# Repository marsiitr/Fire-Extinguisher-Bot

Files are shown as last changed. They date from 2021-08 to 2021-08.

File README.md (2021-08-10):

<p align="justify">
<h1><b>Fire-Extinguisher-Bot</b></h1>
  <h2>Open Projects 2021</h2>
</p>

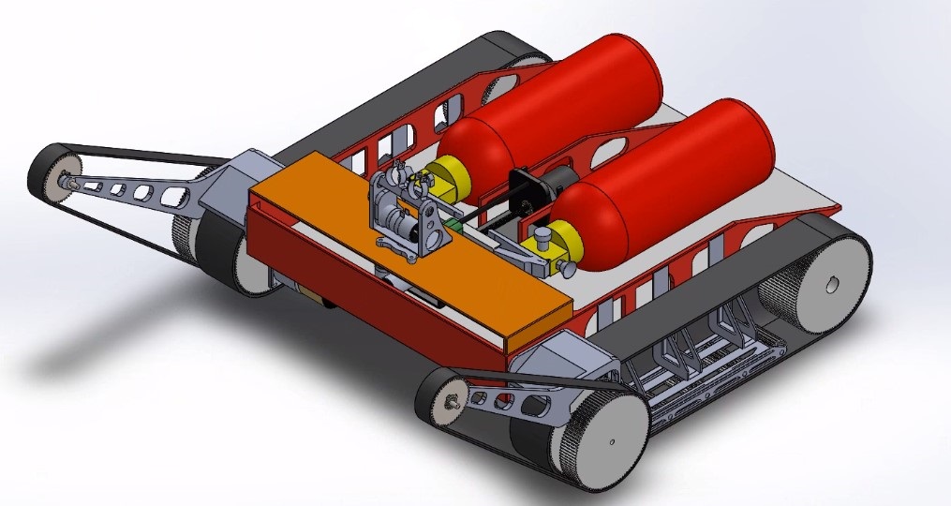
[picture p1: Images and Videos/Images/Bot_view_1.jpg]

<div align="center"><em>Bot View 1</em></div>
<br/>

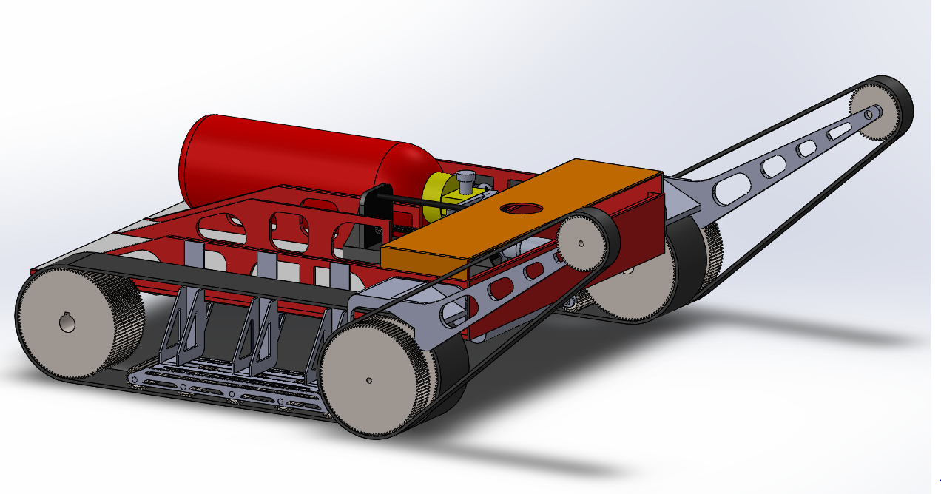
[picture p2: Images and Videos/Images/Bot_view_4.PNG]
Bot Design 2

<div align="center"><em>Bot View 2</em></div>
<br/>
 
<p align="justify">
  <h2>Abstract</h2>
</p>
<p align="justify">
  
- Automatic Fire Extinguisher Robot is a Hardware-based model used to put out the fire during fire accidents automatically. The Bot has features to move in the direction of fire  and extinguish it automatically.
- The Bot finds its applications in rescue operations during fire accidents where concerned authorities can take time to enter the fire-prone areas.
- Development of this autonomus bot using Controllers and image processing can help us to control fire without human inputs.Thus, minimising delays and unavailiblity of services.

</p>
 
<p align="justify">
  <h2>Motivation</h2>
</p>
<p align="justify">
  
The motivation behind this project essentially originated from our desire to learn new things. We can use this autonomous bot in case of laboratories or domestic fires, which can save lives or act as a quick remedy before the concerned authorities arrive. Although this technology is relatively unused in India, it can significantly impact the lives we lose to Fire incidents and our complete dependency on Emergency services.

</p>

<p align="justify">
  <h2>Mechanical Aspect of Design</h2>
</p>
<p align="justify">

The Mechanical Design is explicitly made for significant weight carrying capacity using mild steel as a material having composition of 0.20-0.30% Carbon and Manganese. It is sturdy and reliable and can easily transverse through domestic terrain.
The navigation of this can be both manual and automated. In the automatic mode, it is regulated via a PID Wall Following System.
> ## Wheel Assembly
> 
>The bot uses the Timing Belt Mechanism for the wheel Assembly. It provides an advantage of effortless mobility and significant weight carrying capacity over all the other mechanisms.

<p align="center">
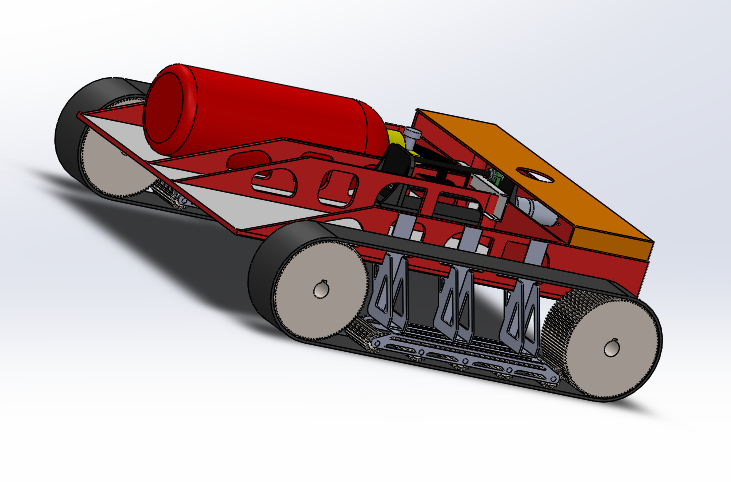
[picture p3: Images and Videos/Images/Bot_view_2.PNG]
  
  <br/><i>Timing Belt and Rollers</i>
</p>

> ## Nozzle Mechanism
> 
>The nozzle is a 2-axis gimbal. This Mechanism can rotate 30 degrees in both horizontal directions and 30 degrees in both vertical directions.

<p align="center">
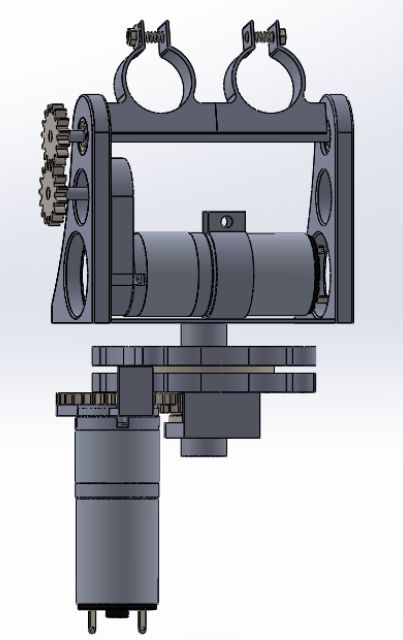
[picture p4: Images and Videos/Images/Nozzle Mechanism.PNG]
  
  <br/><i>Nozzle mechanism</i>
</p>

> ## Handle Pushing Mechanism
> 
>Leadscrew Mechanism can provide a torque of a considerable magnitude and resist the back force applied by the handle. Due to these factors, we use a leadscrew mechanism for handle pushing in our bot.

</p>
<p align="center">
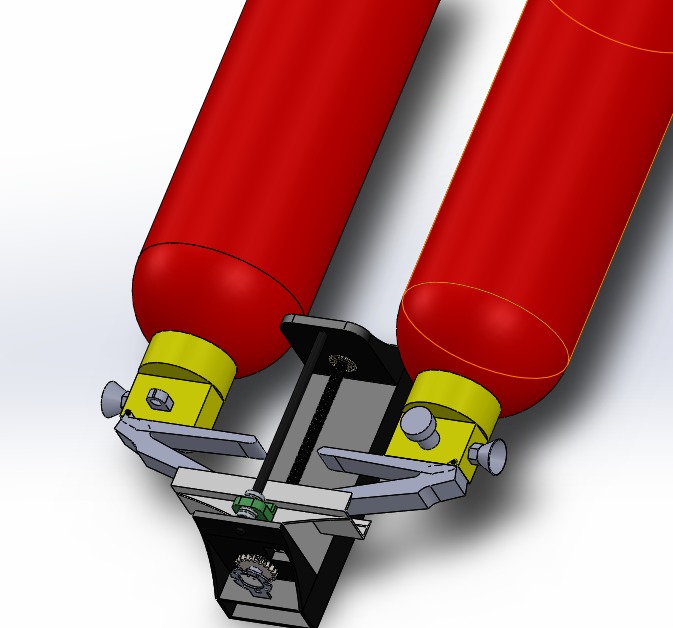
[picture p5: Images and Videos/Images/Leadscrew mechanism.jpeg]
  <br/>
  <i>Leadscrew mechanism</i>
</p>
<p align="justify">
 
> ## Stair Climbing
> 
>The stair climbing mechanism works based on two-timing belts, positioned at an angle of 23 Degrees from the ground. We decided on this angle after a brief round of simulation on coppeliasim.

</p>
<p align="center">
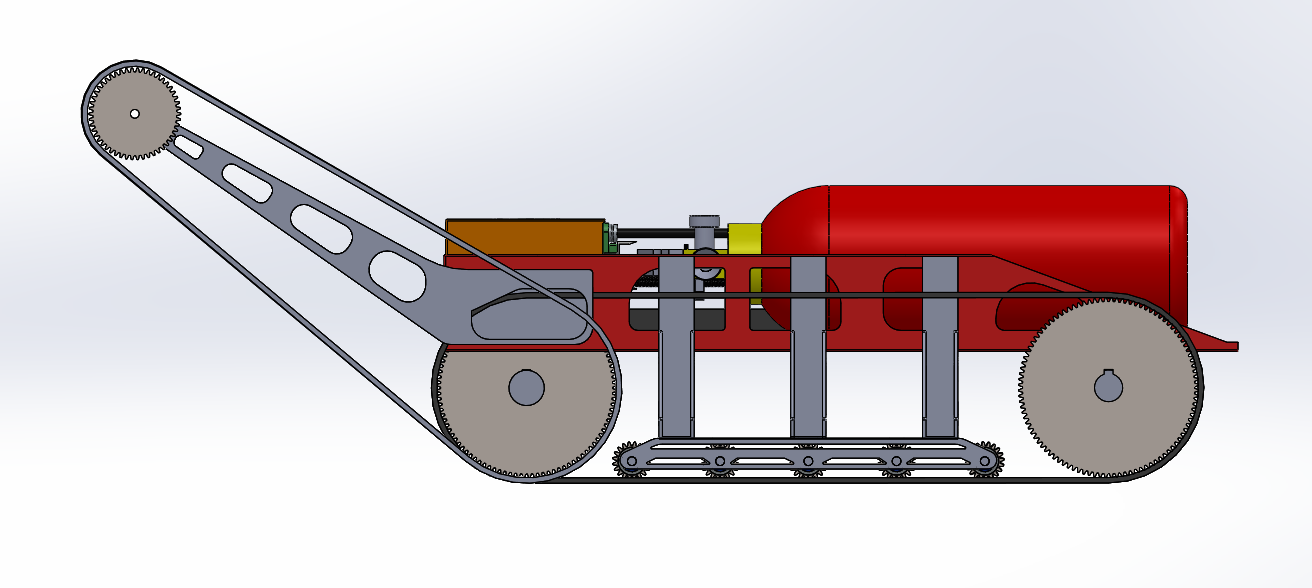
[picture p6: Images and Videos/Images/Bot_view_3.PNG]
  
  <br/><i>Wheel assembly</i>
</p>
<p align="justify">
  <h2>Electrical Aspect of Design</h2>
</p>
<p align="justify">
  
- We used microcontrollers for BOT movement and nozzle movement.

<p align="center">
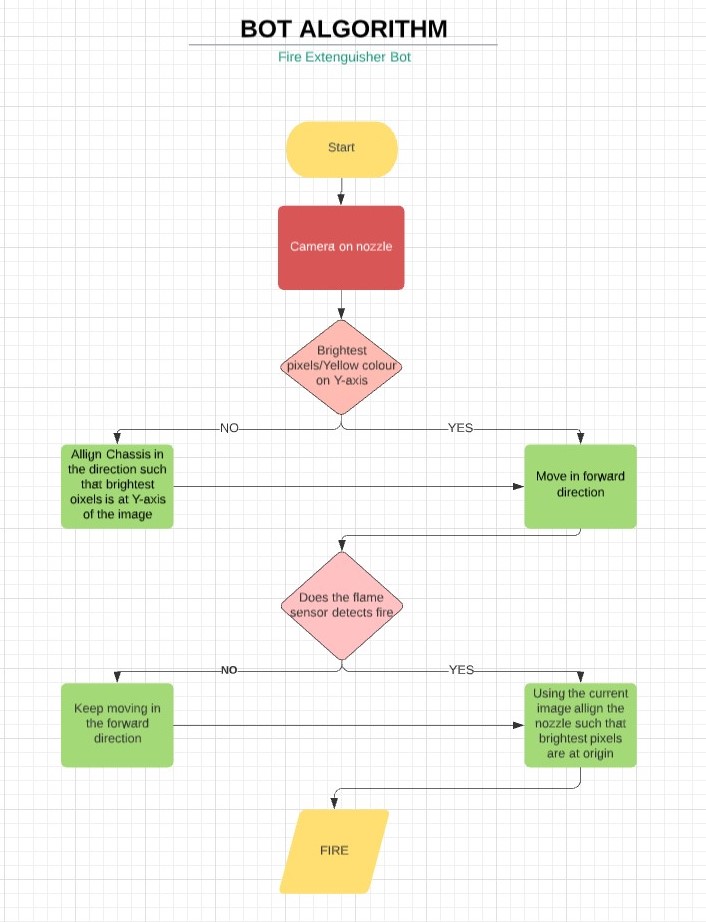
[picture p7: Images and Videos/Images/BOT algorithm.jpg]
  <br/>
  <i>BOT algorithm</i>
</p>

- We also used Ultrasonic distance sensors, Temperature sensors and Flame sensors.
<br/>

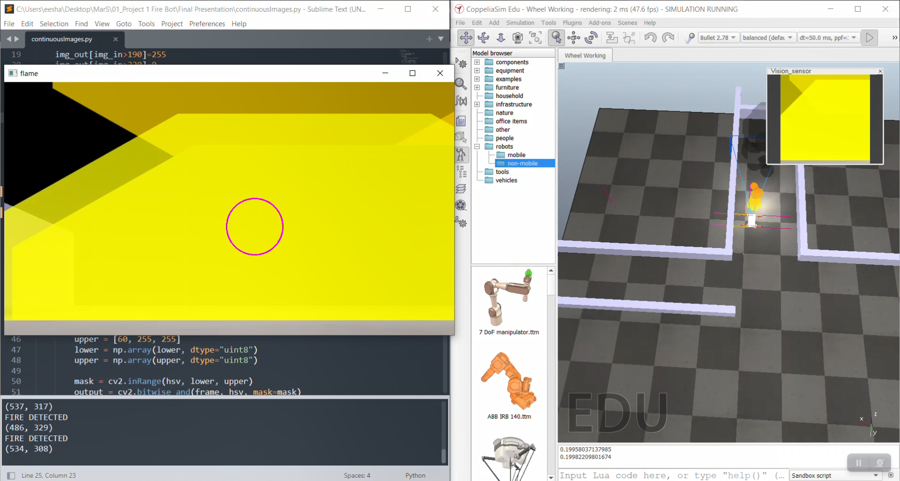
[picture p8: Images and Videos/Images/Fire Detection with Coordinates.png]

<div align="center"><em>simulation</em></div>
<br/>

- For image processing we used camera (*as a Hardware part*). The image processing Software used is OpenCV. The data about the image is fed to OpenCV, where the image is converted to HSV and GreyScale format. Approximate Centre Coordinates of the fire are calculated. This Data is then stored in a text file for the simulation software or Audrino to use.
<br/>

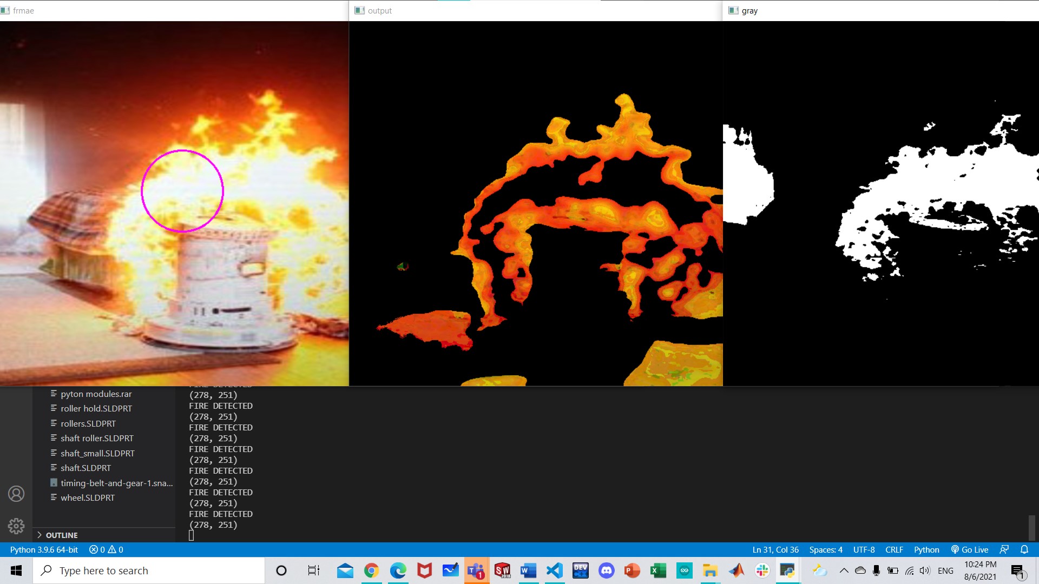
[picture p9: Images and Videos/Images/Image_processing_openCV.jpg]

<div align="center"><em>Image processing</em></div>
<br/>
</p>

<p align="justify">
  <h2>Simulation</h2>
</p>
<p align="justify">
  
For simulation purpose we used the following softwares :-
- Solidworks
    > For mechanical designing of our BOT.
- Tinkercad
    > For simulating Temperature sensor working.
- Coppeliasim
    > For simulating Stair climbing, Wall detection, Wheel PID and Fire detection.
- Python and openCV
    > For Image processing to detect fire and marking that center of fire (high intensity zone) with circle. 

For elaborative explanation, you can refer [here](https://github.com/Ch0ubey/Fire-Extinguisher-Bot/blob/49c68fb09d31af3eed7d412b4f8d0a11268a28de/Simulation/README.md).

</p>
<p align="justify">
  <h2>Applications</h2>
</p>
<p align="justify">
  
- The main objective of the fire extinguishing bot is to search for the fire and put it off. Sensors are used to evaluate the environment in which the bot is operating and allows the bot to adjust actions based on collected data. The buzzer used will be helpful in alarming people about the danger.
- As it is an autonomus bot which uses Controllers and image processing, so it can help us to control fire without human inputs.
- Using this bot we can minimise delays and unavailiblity of services during emergency.
- It can be highly useful in extinguishing fire where probability of explosion is high. For eg. Hotel kitchens, LPG/CNG gas stores, etc.

</p>
<p align="justify">
  <h2>Cost Structure</h2>
</p>

| Components |Amount(INR)  | Quantity |  Cost(INR) |
|--- |:---:|:---: |---:|
| Ultrasonic sensors |  75 |  7 |  525 |
| Temperature sensors |  75 |1 |  75 |
| Flame sensors | 59 |1 |  59 |
| Camera| 300 | 1|  300|
|Arduino UNO|500|1| 500|
|Encoder|1500|1| 1500|
|Dc motors|1500|1| 1500|
|Lead screw|100|1| 100|
|Timing belt (G/GB type) | 400| 1 |400|
|Wheels(lower) |480| 6|2880|
|Wheels(upper)|320 | 2|640|
|3D Printing Filament| 1200|1|1200|
|Fire extinguisher (ABC powder 4kg)|1000|2|2000|
|Mild steel (Body material)|50|2|100|
|**Total Cost**| | |**11,699**|

<p align="justify">
  <h2>Limitations</h2>
</p>

- Takes time to detect fire
- Needs manual assistance while changing the fire extinguishers
- Usable for household fires only
<p align="justify">
  <h2>Future Improvement</h2>
</p>
<p align="justify">
 
* Install cameras in every room
* Link with smoke sensors in the area
* Use custom made cylinders to avoid manual assistance

 </p>
<p align="justify">
  <h2>Team members</h2>
</p>
<p align="justify">

1. [Akanksha Vijayvergiya](https://github.com/Akanksha-247)
2. [Eeshan Punde](https://github.com/eeshanpunde14)
3. [Ganesh Kalanidhi](https://github.com/GaneshK-RKE)
4. [Mritunjay Kumar Choubey](https://github.com/Ch0ubey)
5. [Poreddy Sahith Reddy](https://github.com/sahithreddyporeddy)
6. [Srushti Parbat](https://github.com/SrushtiParbat)

</p>  
<p align="justify">
  <h2>Mentors</h2>
</p>
<p align="justify">

1. [Naman Agarwalla](https://github.com/naman99-agar)
2. [Parul Chaudhary](https://github.com/Parul253)
3. [Shubham Goyal](https://github.com/shubham491981)

</p>
<p align="justify">
  <h2>Refrences link</h2>
</p>
<p align="justify">
  
- [Coppeliasim Tutorial](https://www.youtube.com/watch?v=PwGY8PxQOXY&list=PLjzuoBhdtaXOoqkJUqhYQletLLnJP8vjZ)
- [Solidworks Tutorial](https://youtube.com/playlist?list=PLkMYhICFMsGajeARsY7N1t1jhbtMb1poL)
- [2 axis gimbal](https://www.youtube.com/watch?v=i6UoxhNlr1U)
- [Image processing openCV](https://www.youtube.com/watch?v=Z78zbnLlPUA&list=PLQVvvaa0QuDdttJXlLtAJxJetJcqmqlQq)
- [Coppeliasim Documentation](https://www.coppeliarobotics.com/helpFiles/index.html)

  </p>

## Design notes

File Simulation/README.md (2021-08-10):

<p align="justify">
<h1><b>Running the simulation</b></h1>
  <h2>stair climbing</h2>
</p>

### Installation
<p align="justify">
We used coppeliasim as our simulating software. So, First of all you will have to install it.
</p>

> [CoppeliaSim V4.2.0 rev5 for Windows](https://www.coppeliarobotics.com/files/CoppeliaSim_Edu_V4_2_0_Setup.exe)
### Execution
<p align="justify">

- Download and open the file named "STAIR CLIMBING.ttt".
</p>

  > [STAIR CLIMBING.ttt](https://github.com/Ch0ubey/Fire-Extinguisher-Bot/blob/7c658c72f4b91b798972f8a7e9d713d7e336b766/Simulation/STAIR%20CLIMBING.ttt)

<p align="justify">
  
- Run the simulation by clicking on that play simulation option (As marked in Fig.).
    > <p align="center">
  <br/>
</p>
</p>

## Wheel PID and Fire detection
### Installation

<p align="justify">
  
We used coppeliasim as our simulating software. So, First of all you will have to install it.
</p>

> [CoppeliaSim V4.2.0 rev5 for Windows](https://www.coppeliarobotics.com/files/CoppeliaSim_Edu_V4_2_0_Setup.exe)
<p align="justify">
  
For Image processing part you will have to install python and openCV libraries.
</p>

> [Python 3.9.6 64-bit](https://www.python.org/ftp/python/3.9.6/python-3.9.6-amd64.exe)

> [Tutorial video](https://youtu.be/d3AT9EGp4iw)
### Execution
<p align="justify">
  
- Download and open the file named "Wheel PID and Fire detection.ttt" and "Image processing.py" (Using any IDE).
</p>

   > [Wheel PID and Fire detection.ttt](https://github.com/Ch0ubey/Fire-Extinguisher-Bot/blob/7c658c72f4b91b798972f8a7e9d713d7e336b766/Simulation/Wheel%20PID%20and%20Fire%20detection.ttt)
   
   > [Image processing.py](https://github.com/Ch0ubey/Fire-Extinguisher-Bot/blob/7c658c72f4b91b798972f8a7e9d713d7e336b766/src/Image%20processing.py)
 
 <p align="justify">
  
 - Take any image file and make sure that it should be in the same folder where "Image processing.py" is. Then, paste that image file name on the marked location (Shown in Img.).
    > [Sample image file](https://github.com/Ch0ubey/Self/blob/989c6f968e18636200eb5e8f460e3fbb0165312d/L.jpeg)
    > <p align="center">
  <br/>
</p>
</p>
<p align="justify">
  
- Open that coppeliasim file named "Wheel PID and Fire detection.ttt" and click on that Dummy script option.
      <p align="center">
  <br/>
</p>
</p>
<p align="justify">
  
- Now, change that path location to the samale image you have taken previously.
       <p align="center">
  <br/>
</p>
</p>
<p align="justify">

- Finally, Run the simulation by clicking on that play simulation option (As marked in Fig.).
       <p align="center">
  <br/>
</p>
</p>
<p align="justify">
  
- Also, Run that python file named "Image processing.py" to get centre detection of fire.
</p>

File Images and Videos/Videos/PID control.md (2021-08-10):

# **PID Control**
[PID Control Video](https://drive.google.com/file/d/1zevA3bUyDVg1U9erdCAcblWegYRJz-ra/view?usp=sharing)

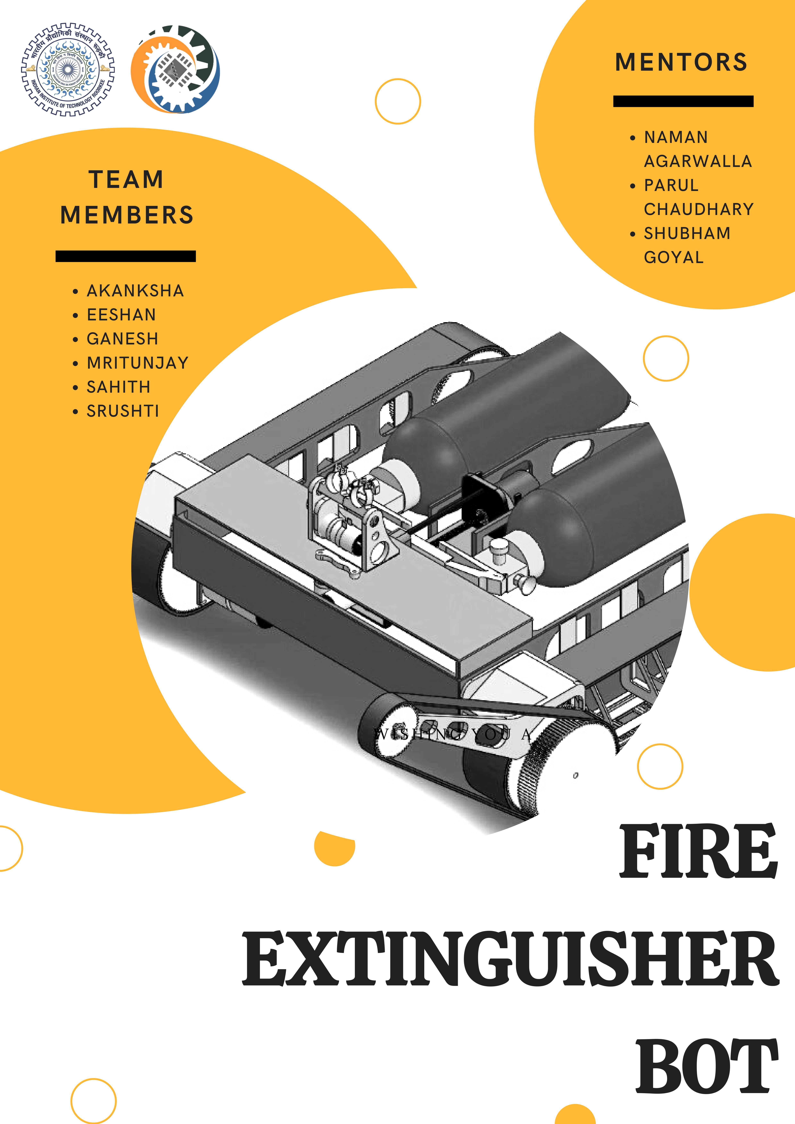
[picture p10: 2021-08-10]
Poster and report/Poster.jpeg

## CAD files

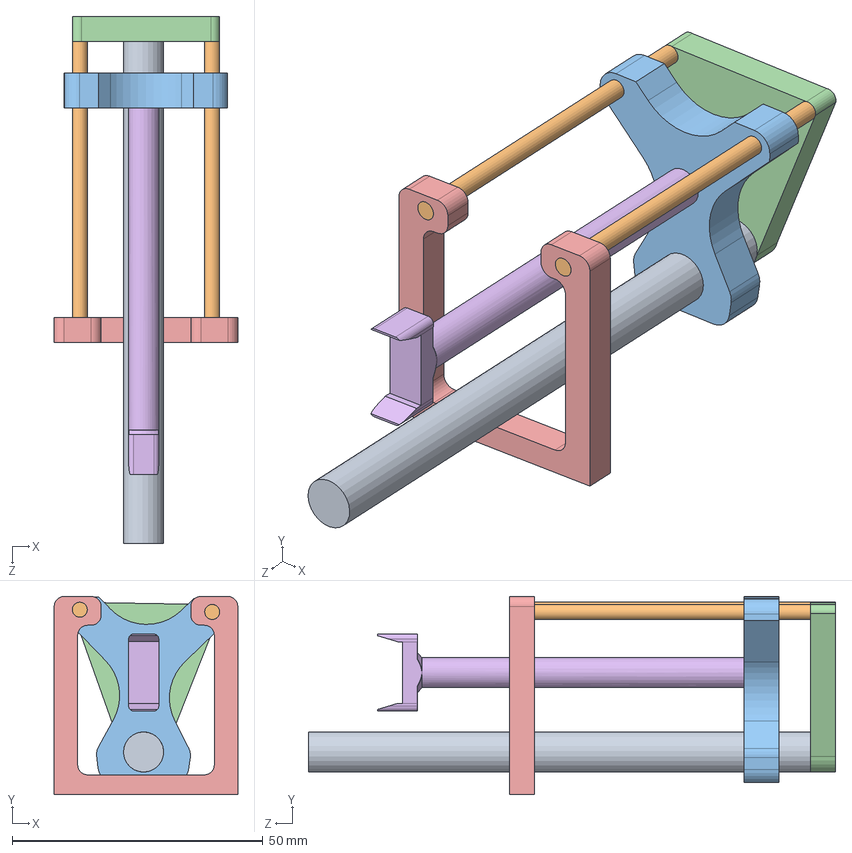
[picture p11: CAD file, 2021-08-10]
Mechanical Design/Bot SolidWorks files/Assem121.SLDASM
36.6 x 39.5 x 105.0 mm
Partscrew
Partrod x 2
Partbase
Part1^Assem121
Part5^Assem121
Partrod33

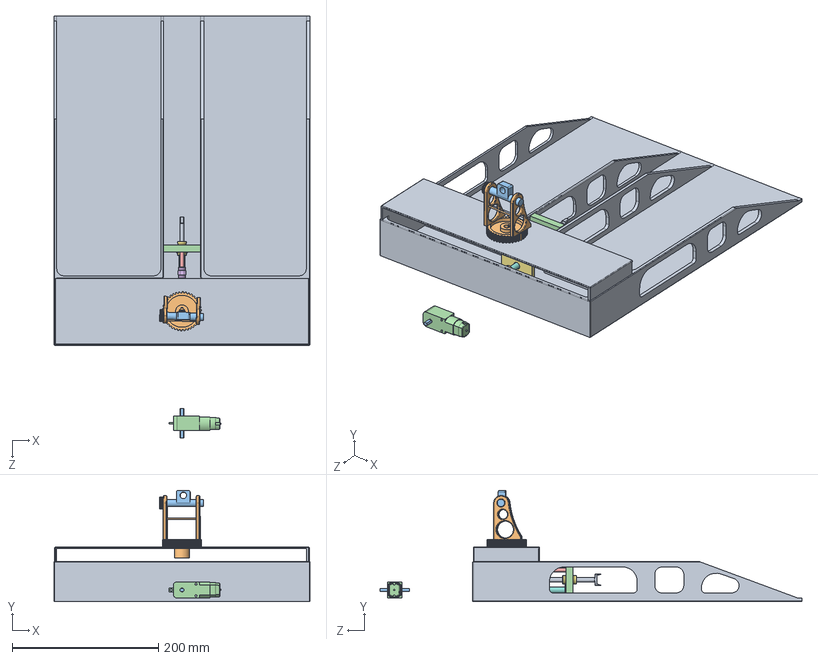
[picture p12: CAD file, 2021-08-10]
Mechanical Design/Bot SolidWorks files/1111.SLDASM
350.0 x 152.2 x 576.4 mm
Part3^1111
Part4^1111
Part5^1111
Part7^1111
Partrod33
Part8^1111
Eje
Motor sin eje
Ball Bearing F695ZZ x 2
ball_bearing_lm5uu
ball_bearing_lm6uu

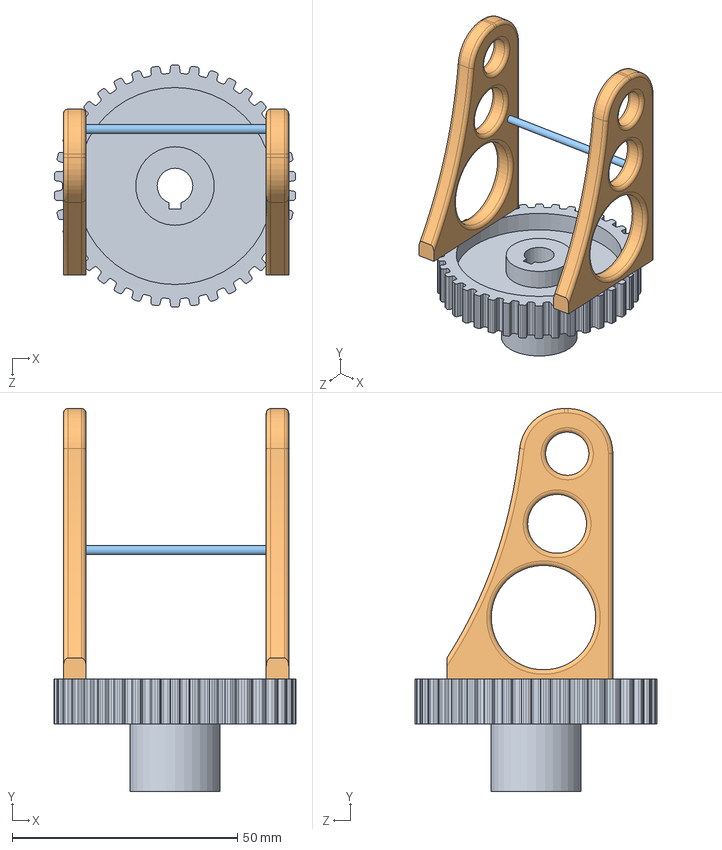
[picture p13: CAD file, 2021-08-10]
Mechanical Design/Bot SolidWorks files/Assem1.SLDASM
53.6 x 85.0 x 53.7 mm

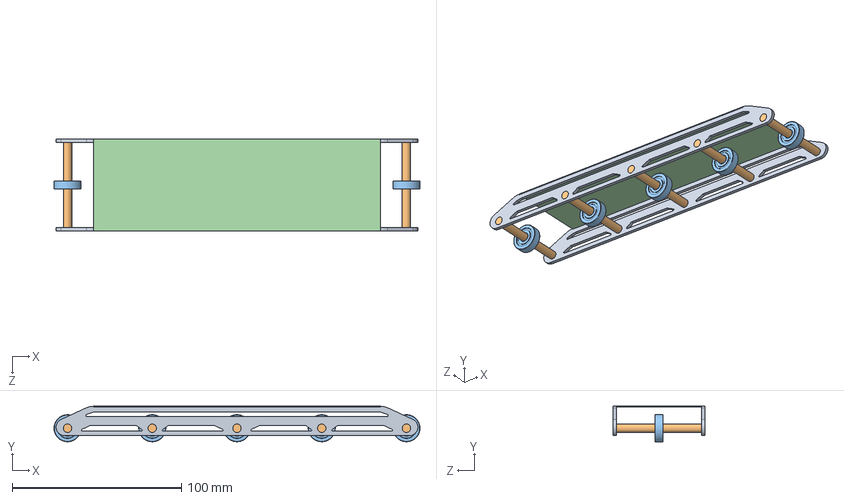
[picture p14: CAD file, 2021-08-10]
Mechanical Design/Bot SolidWorks files/Assem13.SLDASM
216.0 x 21.0 x 54.0 mm
Part16^Assem13
5mm Bearing SKF 625 RS 286-7811 x 5
Part19^Assem13

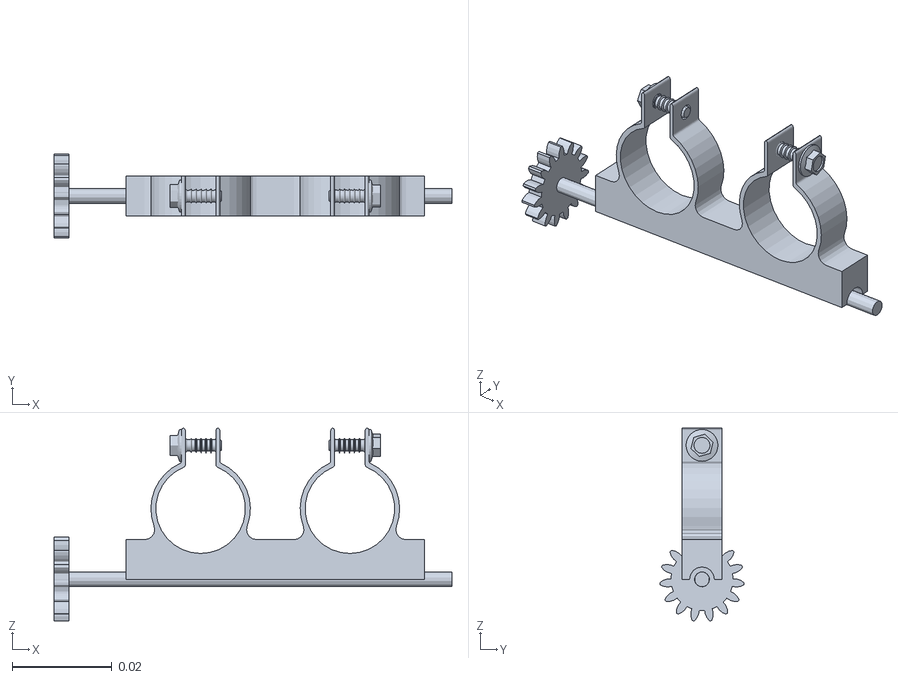
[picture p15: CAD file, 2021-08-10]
Mechanical Design/Bot nozzle/meshes/upper nozzle 0101.STL
0.08 x 0.0169 x 0.0388

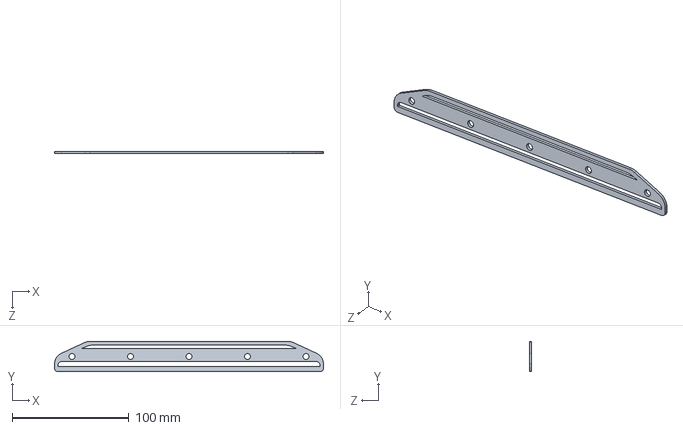
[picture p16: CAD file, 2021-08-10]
Mechanical Design/Bot SolidWorks files/Part15.SLDPRT
230.0 x 26.0 x 2.00 mm

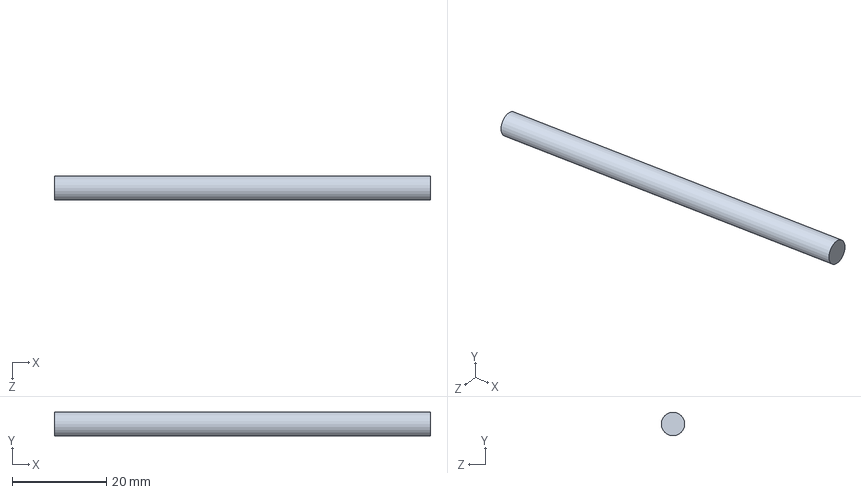
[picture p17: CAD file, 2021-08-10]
Mechanical Design/Bot SolidWorks files/Part2.SLDPRT
80.0 x 5.00 x 5.00 mm

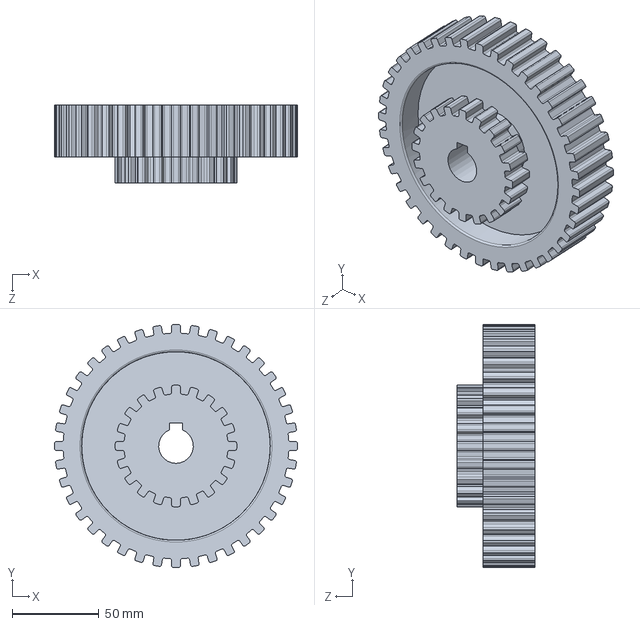
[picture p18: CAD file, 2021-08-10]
Mechanical Design/Bot SolidWorks files/Part10.SLDPRT
140.0 x 140.0 x 45.0 mm

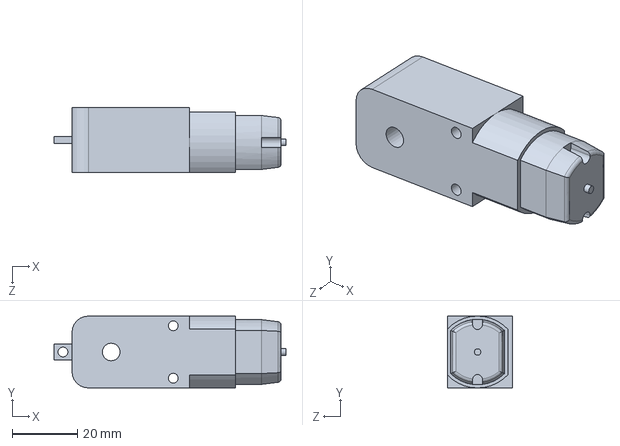
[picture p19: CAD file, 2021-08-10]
Mechanical Design/Bot SolidWorks files/Motor sin eje.SLDPRT
71.0 x 22.0 x 20.0 mm

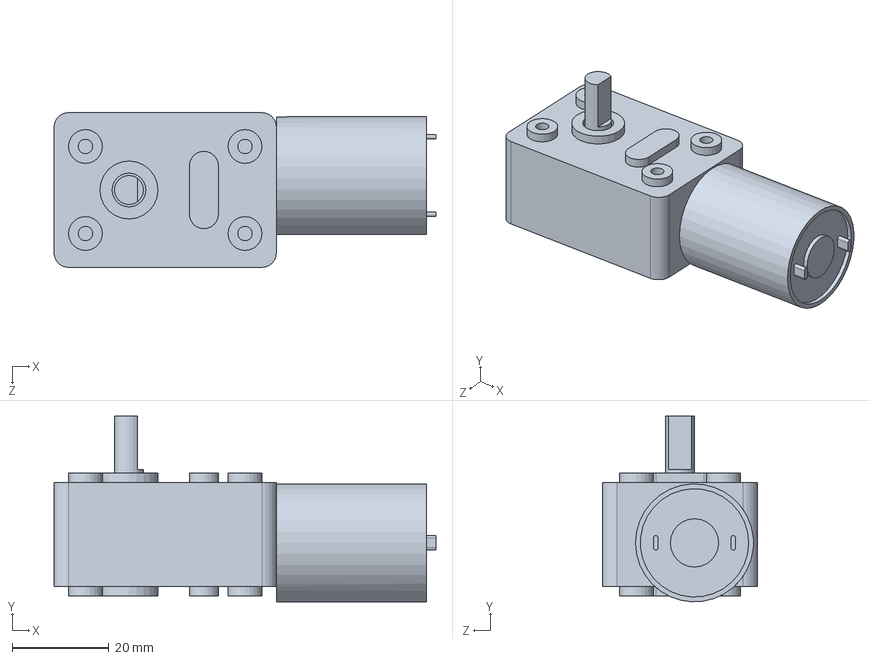
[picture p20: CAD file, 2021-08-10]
Mechanical Design/Bot SolidWorks files/12v_DC_Gearmotor_5-60rpm.SLDPRT
79.0 x 38.4 x 32.0 mm

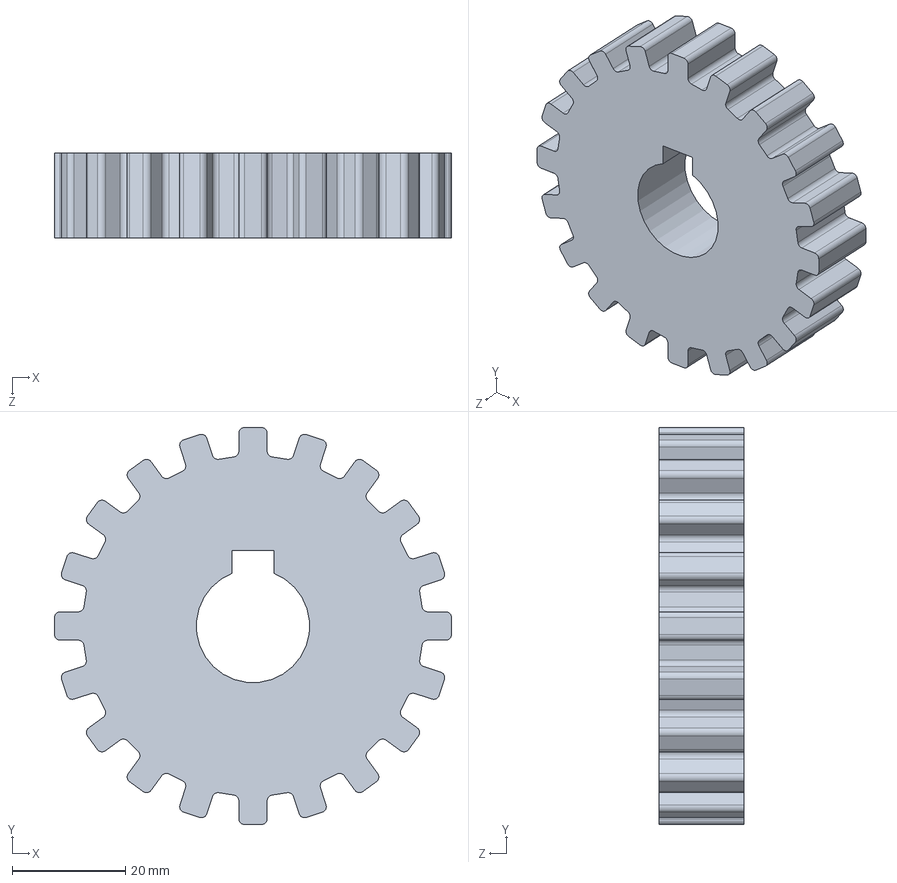
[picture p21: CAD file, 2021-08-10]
Mechanical Design/Bot SolidWorks files/Part9.SLDPRT
70.0 x 70.0 x 15.0 mm

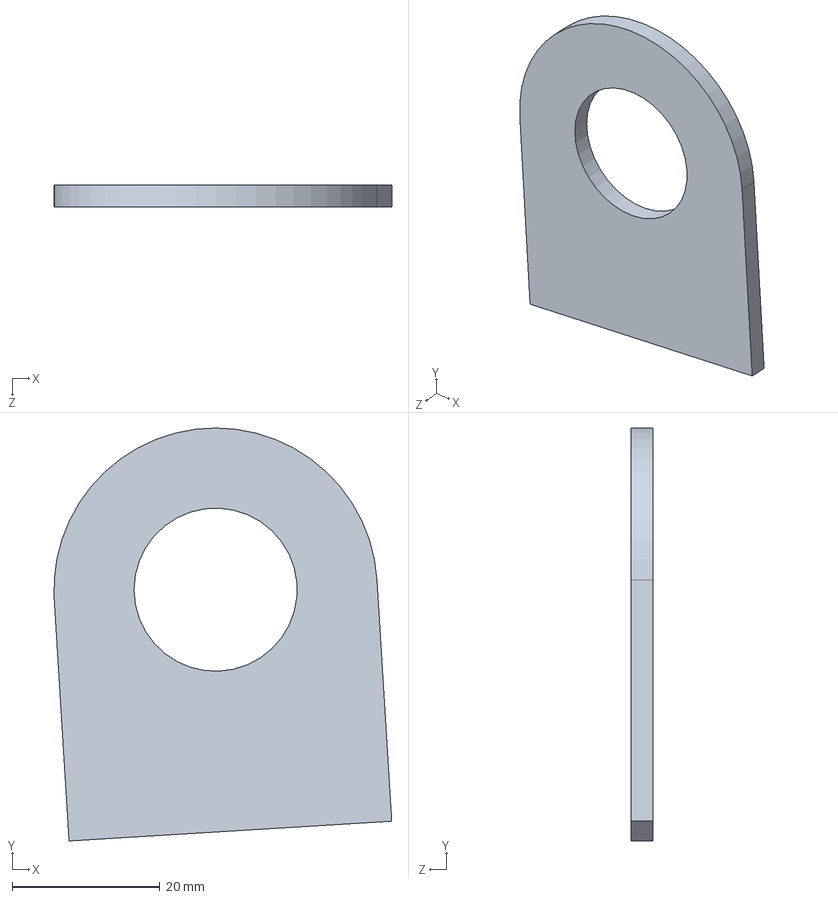
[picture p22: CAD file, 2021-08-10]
Mechanical Design/Bot SolidWorks files/Copy of Part31^Assem12.sldprt
45.7 x 56.0 x 3.00 mm

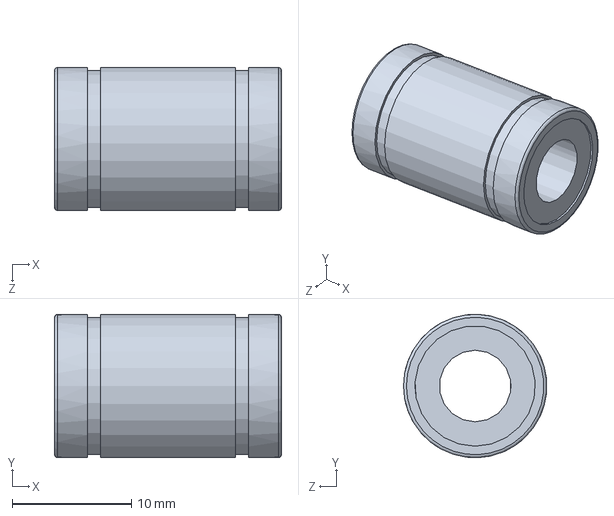
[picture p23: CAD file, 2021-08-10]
Mechanical Design/Bot SolidWorks files/ball_bearing_lm6uu.SLDPRT
19.0 x 12.0 x 12.0 mm

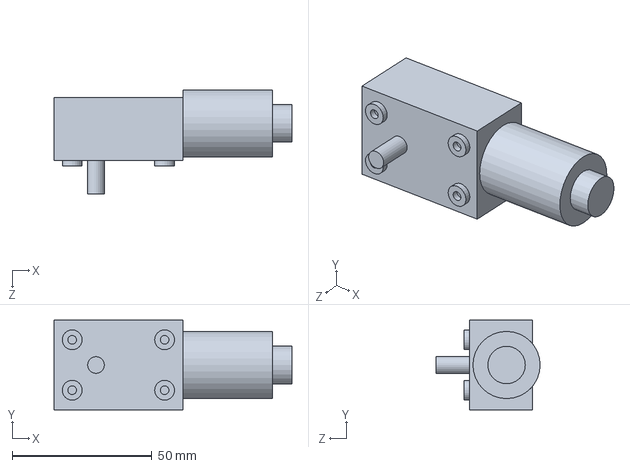
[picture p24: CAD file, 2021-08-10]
Mechanical Design/Bot SolidWorks files/026_Motor DC (1).SLDPRT
85.0 x 32.0 x 37.2 mm

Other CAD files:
Mechanical Design/Bot SolidWorks files/Part1.SLDPRT
Mechanical Design/Bot SolidWorks files/Partrollers.SLDPRT
Mechanical Design/Bot SolidWorks files/Part6.SLDPRT
Mechanical Design/Bot SolidWorks files/Partrod33.SLDPRT
Mechanical Design/Bot SolidWorks files/1111.SLDPRT
Mechanical Design/Bot SolidWorks files/Assem1.SLDPRT
Mechanical Design/Bot SolidWorks files/DC Motor PZ22GR9120R-084BBH - V31111.SLDPRT
Mechanical Design/Bot SolidWorks files/Eje.SLDPRT
Mechanical Design/Bot SolidWorks files/Kormas DC-190w.SLDPRT
Mechanical Design/Bot SolidWorks files/M3 Nut.stp
Mechanical Design/Bot SolidWorks files/M3 x 0.5mm Thread 20mm LONG SOCKET HEAD CAP SCREW.STEP
Mechanical Design/Bot SolidWorks files/MBL3806 (1).step
Mechanical Design/Bot SolidWorks files/MirrorPart20.sldprt
Mechanical Design/Bot SolidWorks files/PG457 DC Motor.SLDPRT
Mechanical Design/Bot SolidWorks files/Part1 (2).SLDPRT
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

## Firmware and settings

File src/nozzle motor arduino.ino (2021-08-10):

#include <Servo.h>
#include <Math.h>

int servoPin_y = 6;  //for rotation in vertical plane
int servoPin_x = 5;  //for rotation in horizontal plane
int pumpPin = 4;

Servo Servo_y;
Servo Servo_x; 

void setup() {
  Serial.begin(9600);
  Serial.setTimeout(100);
  // put your setup code here, to run once:
   Servo_y.attach(servoPin_y);
   Servo_x.attach(servoPin_x);  

   pinMode(pumpPin, OUTPUT);
}

void loop() {
  int counter = 0;
  digitalWrite(pumpPin, HIGH);
  
  float plane_theta=360,z_rotation=360;
  String serialData=Serial.readString(); 
  plane_theta=extractY(serialData);
  z_rotation=extractX(serialData);
  counter = (int)extractZ(serialData);
  delay(100);
  
  
  if(plane_theta < 180 && z_rotation < 180)
  {
    Servo_y.write(round(95+plane_theta)); //mean positions angles adjusted by real world experimentation
    delay(500);
    Servo_x.write(round(100+z_rotation));
    delay(2000);

    if(counter!= 0)
    {
      digitalWrite(pumpPin, HIGH);
      delay(4000);
      digitalWrite(pumpPin, LOW);
      }
    }
}

//buffer string = "X<z_rotation>Y<plane_theta>Z<flame_status>"

int extractX(String data){
  data.remove(data.indexOf("Y"));
  data.remove(data.indexOf("X"),1);
  return data.toFloat();
}

int extractY(String data){
  data.remove(data.indexOf("Z"));
  data.remove(0,data.indexOf("Y")+1);
  return data.toFloat();
}

int extractZ(String data){
data.remove(0,data.indexOf("Z")+1);
return data.toFloat();
}

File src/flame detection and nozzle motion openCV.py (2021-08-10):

import numpy as np
import serial
import time
import cv2
from math import *

# All params are in m. 

# Distance of screen from camera = D
D=1.46

# Height of the camera = H
H= 0.18

# Height of the nozzle = h
h=0.18

# Distance of the nozzle from screen
d=0.20

# m/pixel ratio= D/640 for a distance D of the screen from camera
fact= D/640         

#velocity = 4m/s
u=4

#gravity
g = 9.81

arduino = serial.Serial(port='COM7', baudrate=9600, timeout=0.1) #port number may vary

def find_centre2(white_loc):
    n = len(white_loc)
    #print(n)
    if n<120:
        print("No Flame Detected")
        return  
    arr = np.array(white_loc)
    x,y = np.sum(arr,axis=0)/n
    return (round(y),round(x))


def operate(img):

    img_in = cv2.cvtColor(img,cv2.COLOR_BGR2GRAY)
    img_out = np.zeros(img_in.shape)
    img_out[img_in>230]=255
    return img_out

def find_white_loc(img_in):
    white_loc=[]
    m,n = img_in.shape
    for i in range(m):
        for j in range(n):
            if img_in[i,j]==255:
                white_loc.append([i,j])
    return white_loc

def plane_theta(centre):
        ## coordinates with respect to camera
        x = centre[0]*fact
        y = centre[1]*fact

        ## coordinates with respect to nozzle. Obtained by shifting of origin
        X = sqrt(d**2+(x)**2)
        Y = y + H - h
        print("X:",X, "Y: ", Y)

        Q1 = ( atan( ( (u**2) + sqrt( u**4 - 2*Y*g*u**2 - (g**2)*(X**2) ) ) / (g*X) ) ) * 180/3.1415
        Q2 = ( atan( ( (u**2) - sqrt( u**4 - 2*Y*g*u**2 - (g**2)*(X**2) ) ) / (g*X) ) ) * 180/3.1415

        if (abs(Q1)<abs(Q2)):
            angle = Q1
        else:
            angle = Q2
        print("Vertical Angle is : ",angle) 
        return angle

def z_rotation(centre):

	## coordinates with respect to camera
        x = centre[0]*fact
        y = centre[1]*fact
        

        # coordinates with respect to nozzle. Obtained by shifting of origin
        X = x
        Y = y + H - h

        angle=(atan(X/d))*180/3.1415
        
        print("Horizontal Angle is :", angle)
        return angle
    
while True:
        video = cv2.VideoCapture(0)
        ret,frame = video.read()
        if ret== False:
            break
    
        frame = cv2.resize(frame, (960, 540)) 
 
        blur = cv2.GaussianBlur(frame, (21, 21), 0)
        hsv = cv2.cvtColor(blur, cv2.COLOR_BGR2HSV)
 
        lower = [18, 50, 50]
        upper = [35, 255, 255]
        lower = np.array(lower, dtype="uint8")
        upper = np.array(upper, dtype="uint8")

        mask = cv2.inRange(hsv, lower, upper)
        output = cv2.bitwise_and(frame, hsv, mask=mask)
        no_red = cv2.countNonZero(mask)
        
        img = np.copy(frame)
        mask = operate(frame)
        white_loc = find_white_loc(mask)
        centre = find_centre2(white_loc)

        if int(no_red) > 15000:
            print("FIRE DETECTED")
            print(centre)
            if int(centre[0]) > 0 :
                print("1")
            if int(centre[0]) == 0 :
                print("1")
            if int(centre[0]) < 0 :
                print("-1")

        cv2.circle(frame,centre,60,(255,0,255),2)
        cv2.imshow('frmae',frame)    
        cv2.imshow('output',output)
        if centre!=0:
	        adj_centre=(centre[0]-320,-centre[1]+240)
	        if centre!= None:
	            print(adj_centre)
	            img = cv2.circle(img,centre,40,(255,0,0),3)
	            img = cv2.circle(img,centre,0,(255,0,0),5)
	            img = cv2.circle(img,(320,240),0,(255,0,0),5)

        
        else:
            arduino_out="X"+str(360)+"Y"+str(360)+"Z"+str(0)
        
        arduino.write(bytes(arduino_out, 'utf-8'))
        arduino.flush()
        time.sleep(0.5)
        print(arduino_out) 

        if cv2.waitKey(1) & 0xFF == ord('q'):
            break
    
video.release()
cv2.destroyAllWindows()

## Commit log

2021-08-07 Create PID control.md
2021-08-07 Update nozzle motor arduino.ino
